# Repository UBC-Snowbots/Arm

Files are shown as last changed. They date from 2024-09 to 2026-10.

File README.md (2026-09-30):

# Arm – UBC Rover 

**CAD Models and Designs for the UBC Rover Arm**

## Table of Contents
1. [About](#about)  
2. [Repository Structure](#repository-structure)  
3. [Getting Started](#getting-started)  
4. [CAD Workflow & Tools](#cad-workflow--tools)  
5. [Contributing](#contributing)  
7. [Acknowledgments](#acknowledgments)  
8. [Contact](#contact)

---

## About
This repository contains the CAD models and design files for the 6 axis robotic arm of the UBC Rover, developed by the UBC Rover Arm subteam. These files are used for design iteration, simulation, and manufacturing preparation.

---

## Repository Structure
```
Arm/
├── Arm 2024-2025/       # CAD files for the 2024-2025 arm
├── Arm 2025-2026/       # CAD files for the 2025-2026 arm
├── Drawings/            # Technical drawings, schematics, and exports
├── .gitignore
└── README.md            # Project overview and documentation
```

- **Arm 2025-2026/**: Latest CAD sources & URDFs.
- **Drawings/**: Finished outputs such as PDFs, DXFs, and manufacturing diagrams.

---

## Getting Started

### Prerequisites
- CAD Software compatible with source files, currently using Solidworks 2023.
- CAD viewer or PDF reader to view exported files without full CAD tools.

### How to Use
1. Clone the repository:
   ```bash
   git clone https://github.com/UBC-Snowbots/Arm.git
   cd Arm
   ```
2. Navigate to:
   - `Arm 2024-2025/` for the latest CAD work.
   - `Drawings/` for schematics and PDFs.
3. Open files in your CAD software or a viewer.
   
Or, download the github desktop app.

---

## CAD Workflow & Tools
- Primary CAD platform: Solidworks 2023.
- Standard modeling practices:
    - Use hole wizard where applicable (tapped & clearance holes)
    - **For manufacturing fits see below**
      - For close fits (bearings, bushings, etc) in 3D prints, use ~1mm extra for tolerances.
      - For looser fits (a cover to slide over something, like a sleeve) in 3D prints, use ~1.5mm extra.
      - When machining, we can get ~±0.1mm pretty easily. If necessary, maybe ±0.05mm. If you're going to machine it you can go as tight as you want.
    - When making assemblies, please include fasteners, and when making threads, make the threads basic to help the assembly run faster.
    - Make sure all sketches are fully defined
    - Use equation tables & add multiple configurations if necessary
- When saving a file for 3D printing, save it as a .STEP file for higher print quality
- Give files descriptive names & ensure they're in the proper folders
---

## Contributing
Please push your changes & send a message to the discord when you do. This helps us keep track of what's happening and prevents peoples work from being lost. 
### Through command prompt
1. Make the change and ideally only edit the file you need to edit
2. If you see a file you didn't mean to edit, or just moved the camera around in an assembly, unselect that file
3. Commit with a clear message:
   ```bash
   git commit -m "Add <feature>: description"
   ```
4. Merge with main branch
5. Send a message to the discord w the files you changed

### Through Github Desktop
1. Make the change and ideally only edit the file you need to edit
2. Open the github desktop app 
3. If you see a file you didn't mean to edit, or just moved the camera around in an assembly, unselect that file
4. Write a semi-detailed description
5. Push the changes AND merge to main branch
6. Send a message to the discord w the files you changed

Ensure new CAD files include notes or documentation

---

## Acknowledgments
This was not designed by a single person, it's a multi year project with influences from the start of the team. Thanks to all current & past Rover arm team members.

Thanks to the entire team, especially software for making the arm work & chassis for making it useful. 

---

## Contact
For questions or feedback:
- **Arm Team Leads 2026-27** – *(William Banquier: william.banquier@gmail.com, Matt Yung: yungco44@gmail.com)*
- UBC Rover GitHub: [https://github.com/UBC-Snowbots](https://github.com/UBC-Snowbots)

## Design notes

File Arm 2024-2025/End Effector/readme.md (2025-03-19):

## EE Github Documentation

### Files

- Tool Changer Prototypes
    - Ball Bearing Mech Changer
    - Smartshift Mechanical Tool Changer
    - Magnet Sensor A1301-2
- Big Gripper
	- Gripper End Effector
	- Derivative of Last Year's End Effector
	- Folder also contains copy of 2024 (old) end effector -> as in the entire CAD
	- Folder also has a copy of the maxxon motor 
- Percision End Effector
	- CoreXY 
		- CoreXY for the end effector
		- Contains all housing and CAD 
	- Gripper Mechanism
		- Contains cad for the gripper mechanism
		- Contains cad for the actuator ("poking thingy" folder)

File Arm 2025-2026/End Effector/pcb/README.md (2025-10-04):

# End Effector PCB Sub-directory 

## Goals: 
1. Hold relevant PCB files for the end effector 
2. Store relevant PCB CAD files for the overall arm CAD
3. Store end effector testing / rnd PCB projects

## Directories:
[/EE-PCB](./EE-PCB)

[/CAD](./CAD)

[/RND](../../RnD/PCB)

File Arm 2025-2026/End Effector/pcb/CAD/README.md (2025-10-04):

## End Effector PCB CAD Folder 

Please note the CAD files that are here + where they are used

## CAD-LIST
- 
-
-
-
-

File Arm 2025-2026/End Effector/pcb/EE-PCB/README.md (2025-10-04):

This is a parent folder for the PCB files used within the end effector

## List of Project and Where the Board is Used on the EE
-
-
-
-
-
-
-

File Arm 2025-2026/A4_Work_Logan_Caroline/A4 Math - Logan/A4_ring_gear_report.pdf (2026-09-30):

## A4 Ring Gear Analysis

Note: the excel file is attached with this. Alter the red highlighted cells as needed.

### Assumptions

1. A4 is constrained, that is: no axial or radial loading on the motor when it is not rotating
2. Low friction
3. The center of mass of L2, the end effector, and the load are along A4

In short, I assume that A4 has to overcome the inertia of its rotor, L2, EE and the load, but it does not face any significant resisting torques from gravity or friction.

### Derivation

Let N = total gear ratio on A4 motor

Let J = total moment of inertia felt by the rotor

From the rotor:

Trotor = Jαrotor

The moment of inertia of the load felt by the rotor is reduced by a factor N² , thus:

Trotor =

Jrotor +

Jload
N²
αrotor | (1)

Also, due to the gear reduction:

αL2 =

αrotor
N

(2)

αL2 =

NTrotor

N²Jrotor + Jload

### Plugging in the Numbers

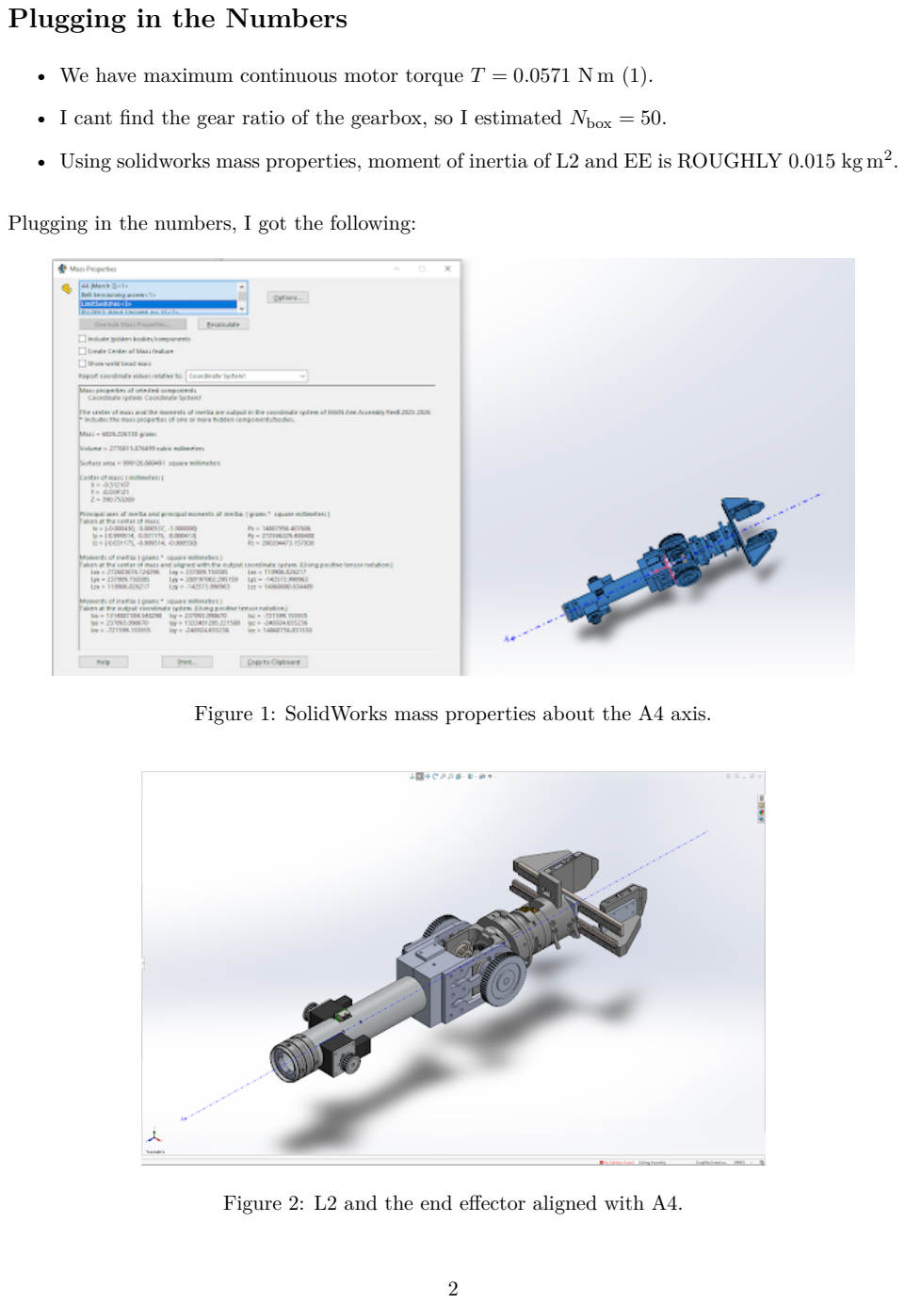
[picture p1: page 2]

- We have maximum continuous motor torque T = 0.0571 N m (1).
- I cant find the gear ratio of the gearbox, so I estimated Nbox = 50.
- Using solidworks mass properties, moment of inertia of L2 and EE is ROUGHLY 0.015 kg m² .

Plugging in the numbers, I got the following:

Figure 1: SolidWorks mass properties about the A4 axis.

Figure 2: L2 and the end effector aligned with A4.

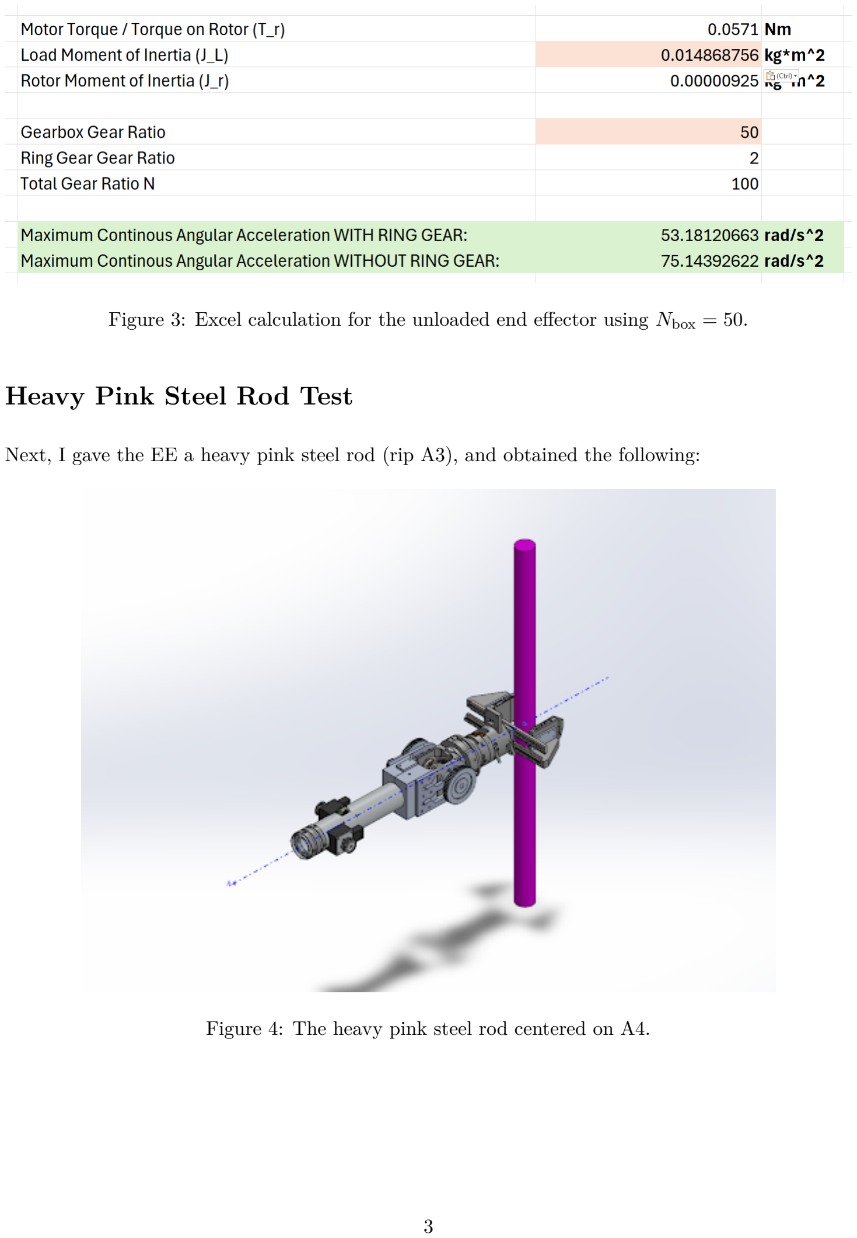
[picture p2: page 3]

Figure 3: Excel calculation for the unloaded end effector using Nbox = 50.

### Heavy Pink Steel Rod Test

Next, I gave the EE a heavy pink steel rod (rip A3), and obtained the following:

Figure 4: The heavy pink steel rod centered on A4.

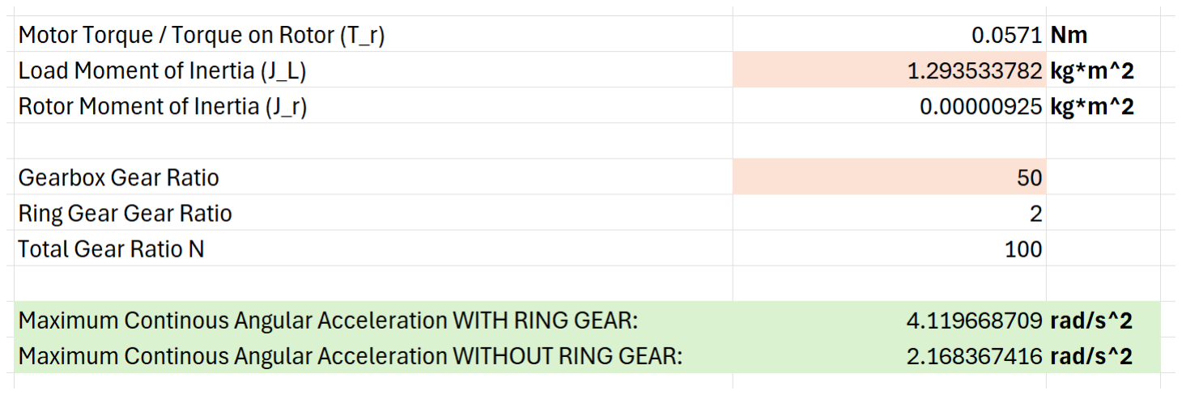
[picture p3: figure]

Figure 5: Excel calculation with the heavy steel rod using Nbox = 50.

### Conclusion

As long as Ngearbox ≥ 29, A4 is actually “quicker” WITHOUT the ring gear when the end effector is unloaded. However, the 2:1 ring gear begins to support A4 angular acceleration at higher loads.

With a known Ngearbox, one could easily use the excel calculator to pinpoint the exact load moment of inertia at which the ring gear becomes a useful support (ignoring the extra complexity).

### The Dangerous Assumption

Now, the astute among you may realize that assumption 3 is quite dangerous. For example, what if the pole was held like this?:

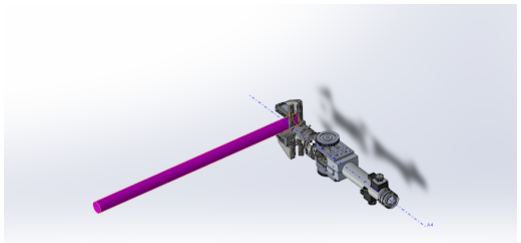
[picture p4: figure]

Figure 6: The same rod held asymmetrically about A4.

The rod moves the large center of mass away from A4, creating a resistive gravitational torque on A4. The A4 motor would be cooked.

The math here is pretty simple: by sacrificing the ring gear which has a gear ratio of 2:1, we are exactly reducing the maximum torque output of L2 by this factor of 2. In other words, the maximum asymmetrical load would halve, so to speak.

More specifically:

With a stall torque of 0.263 N m (1), the resistive torque on L2 can be no more than

τL2,max = (0.263 N m) × N,

where N is the total gear ratio from the motor to L2. For example, after removing the 2:1 ring-gear stage, N = 50, so this is about a single apple 9 meters away horizontally from the axis.

TL;DR

By removing the 2:1 ring-gear stage:

Pros:

1. The unloaded A4 angular acceleration is higher, ie A4 rotation is quicker
2. The theoretical maximum A4 angular speed is doubled for the same motor speed
3. Simpler design
4. No more unmeshing of ring gear due to A4 offset
5. Less backlash

Cons:

1. At higher loads, A4 angular acceleration is lower (exact load can be calculated in the attached spreadsheet)
2. The maximum allowable resistive torque on L2 due to friction and gravity is exactly halved. Likely to only be a problem for heavy asymmetric loads, such as distant apples.

Reference:

1. https://www.maxongroup.com/maxon/view/product/200142

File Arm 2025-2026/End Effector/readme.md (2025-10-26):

## End Effector :eyes:

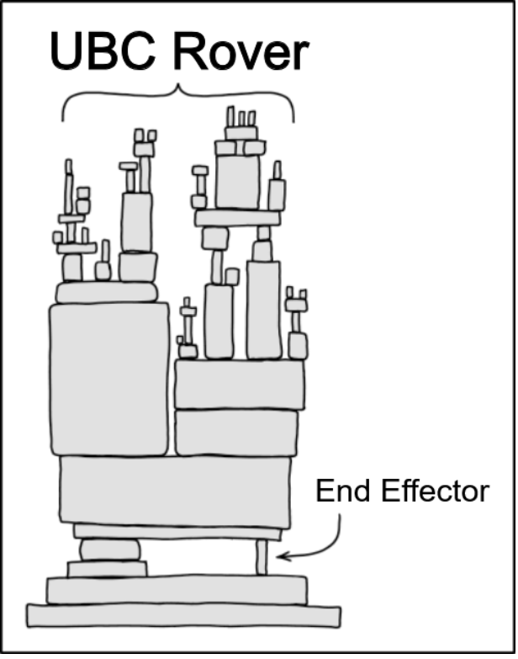
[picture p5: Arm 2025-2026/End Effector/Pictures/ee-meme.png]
EE Meme


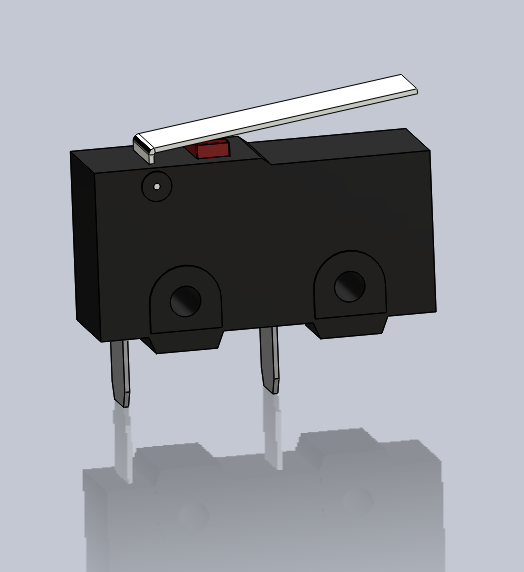
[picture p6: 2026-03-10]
Arm 2025-2026/End Effector/Polar Precision/OTS/Limit Switch/Limit A1.PNG

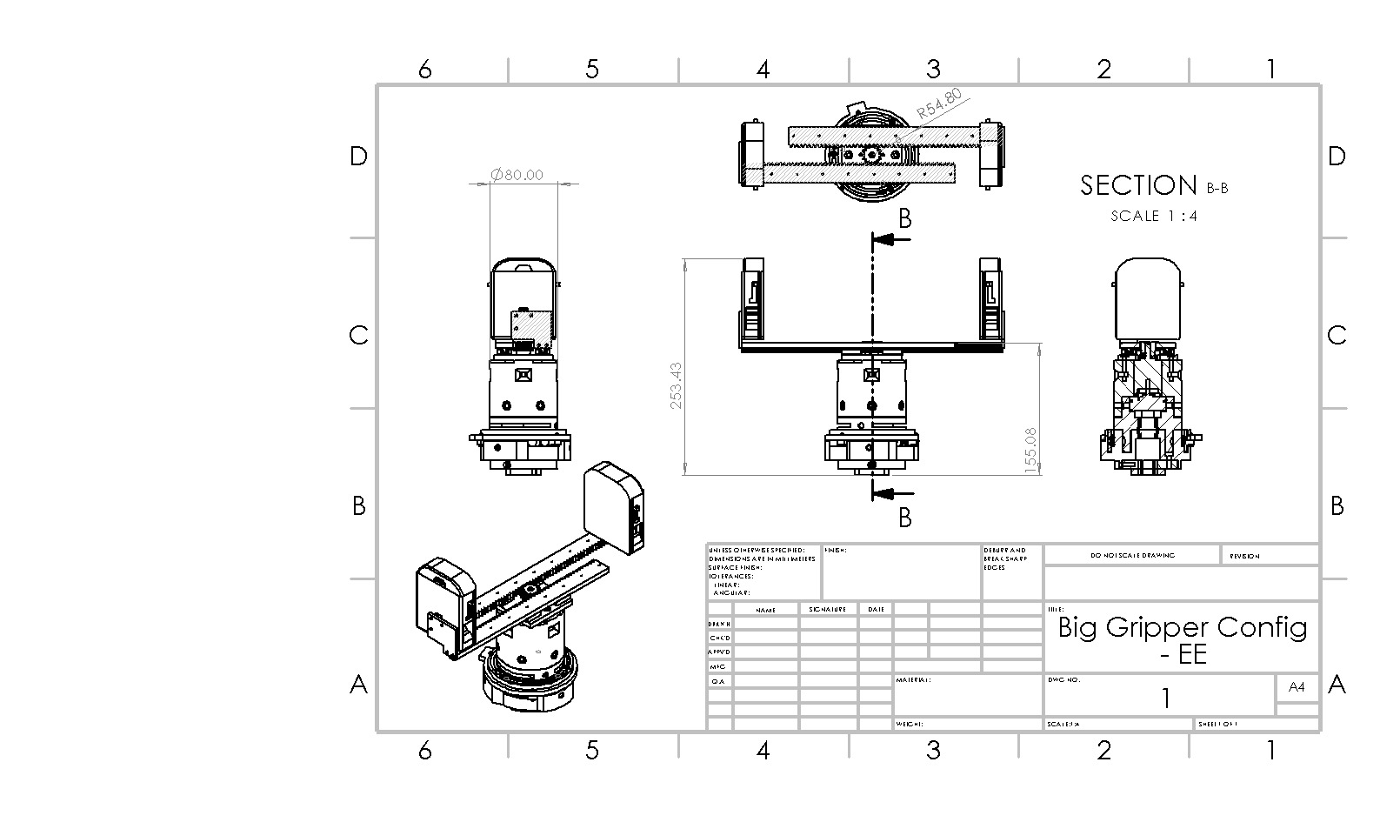
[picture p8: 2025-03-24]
Arm 2024-2025/End Effector/Tool Changer Prototypes/ball-bearing-mech-changer/Big Gripper Drawing.JPG

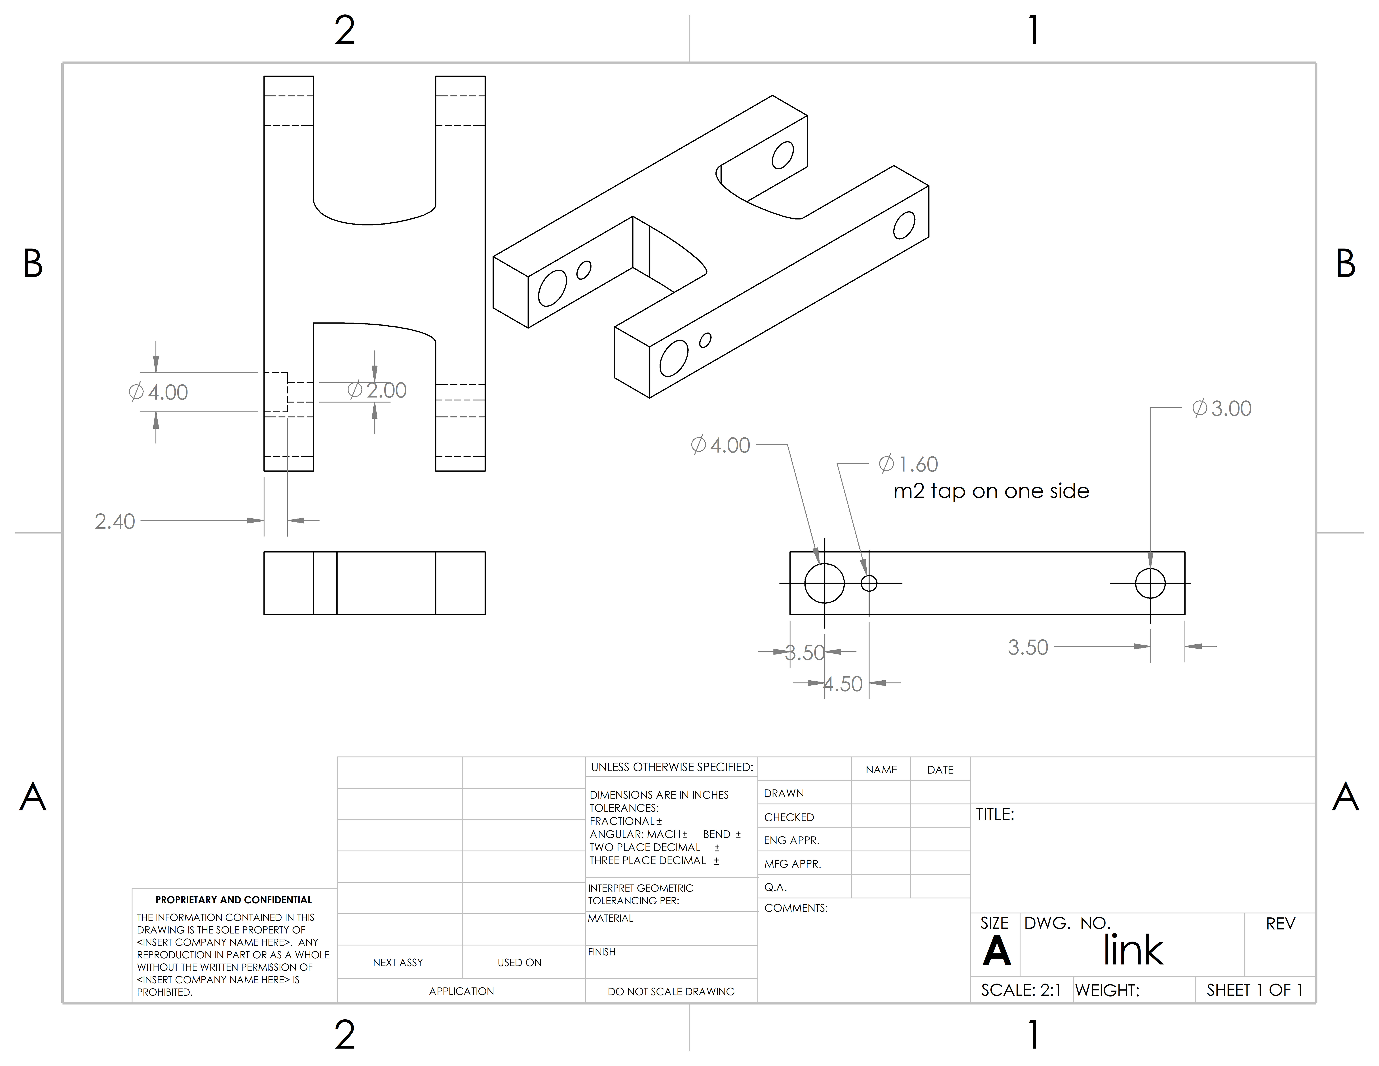
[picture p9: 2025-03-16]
Arm 2024-2025/End Effector/Precision End Effector/Gripper mechanism/waterjet/link.JPG

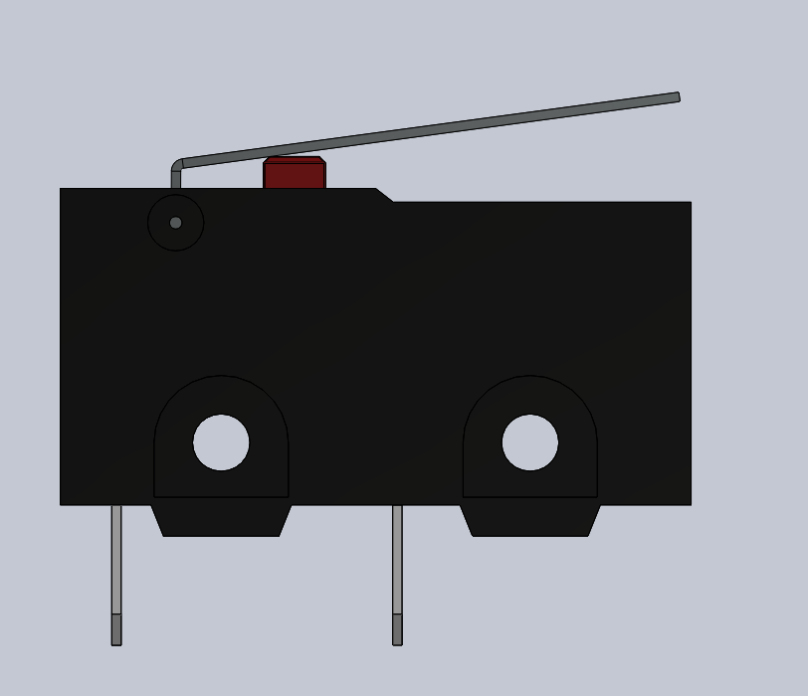
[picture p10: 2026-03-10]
Arm 2025-2026/End Effector/Polar Precision/OTS/Limit Switch/Limit A2.PNG

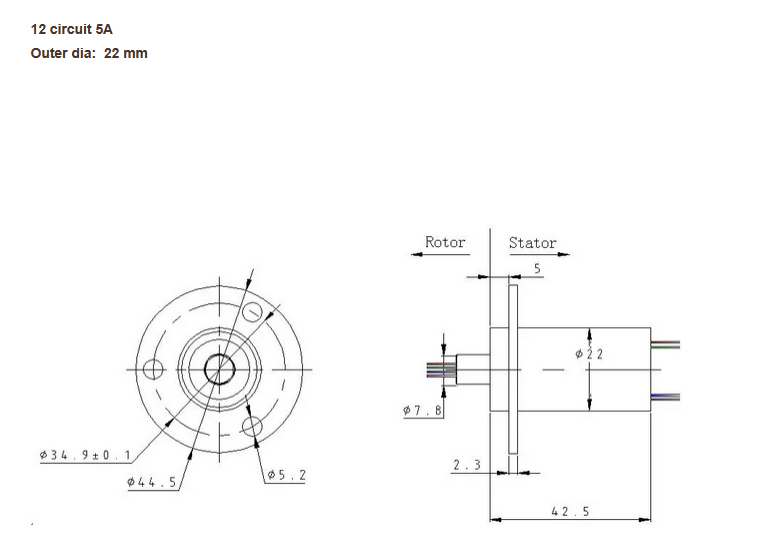
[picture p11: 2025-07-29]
Arm 2024-2025/Link 2/12circuit 5A Slip Ring.png

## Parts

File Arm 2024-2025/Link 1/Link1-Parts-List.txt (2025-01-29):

Corner Mount thing:

https://www.mcmaster.com/4844N108/

Ball-bearing for link 1 A2 harmonic drive:

https://www.mcmaster.com/6656K227/

Bearing for support A2:

https://www.mcmaster.com/5972K168/

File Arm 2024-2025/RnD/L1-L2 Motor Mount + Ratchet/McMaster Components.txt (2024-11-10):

Corner Mount thing:

https://www.mcmaster.com/4844N108/

Shaft Couple 6.35mm to 12mm:

https://www.amazon.ca/uxcell%C2%AE-Coupling-Diameter-Aluminum-Connector/dp/B06X9RZ1QC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

Ratchet gear:
https://www.mcmaster.com/6283K64/

Pawl:

https://www.mcmaster.com/6283K72/

Bushing:

https://www.mcmaster.com/6658K11/

Spring:

https://www.mcmaster.com/94125K414/

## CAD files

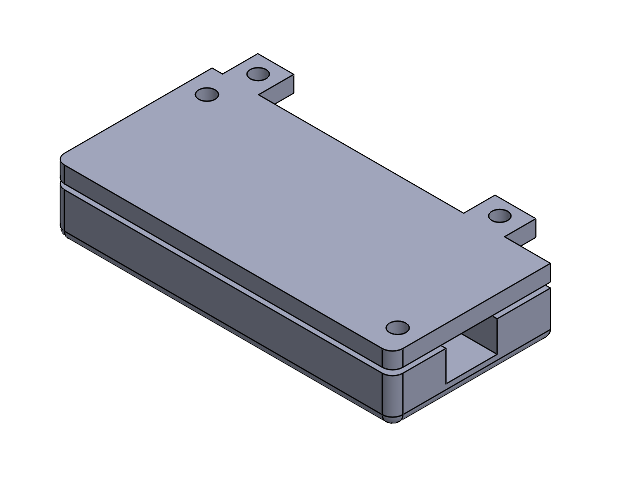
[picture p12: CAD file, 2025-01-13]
Arm 2024-2025/End Effector/Big Gripper/2024 End Effector/esp32/esp32_container_assembly.SLDASM
esp container
esp metal top

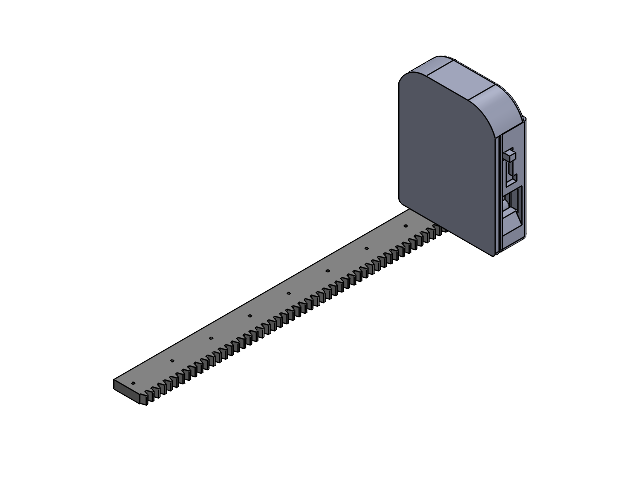
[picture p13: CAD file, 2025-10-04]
Arm 2024-2025/End Effector/Big Gripper/2024 End Effector/Fingers.SLDASM
SR1.5-300_On
Finger_Backing
base3
opener3 x 2
wall3 x 2
thing_inside_wall_3 x 2
top3
detachable3

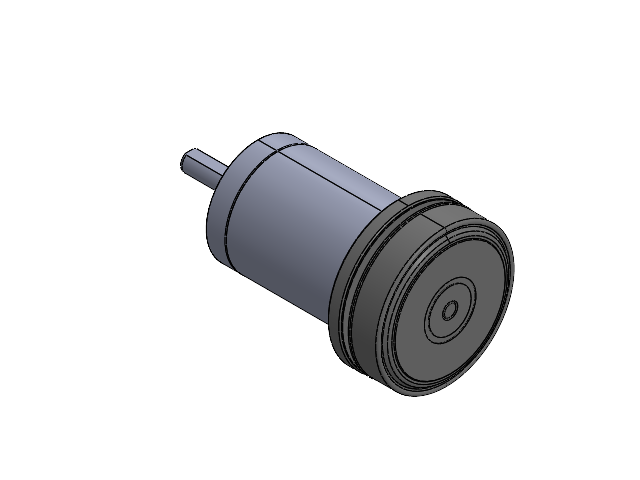
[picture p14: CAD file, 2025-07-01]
Arm 2024-2025/End Effector/Big Gripper/Big Gripper Motor Assy.SLDASM
Big Gripper Gearbox
Big Gripper Motor

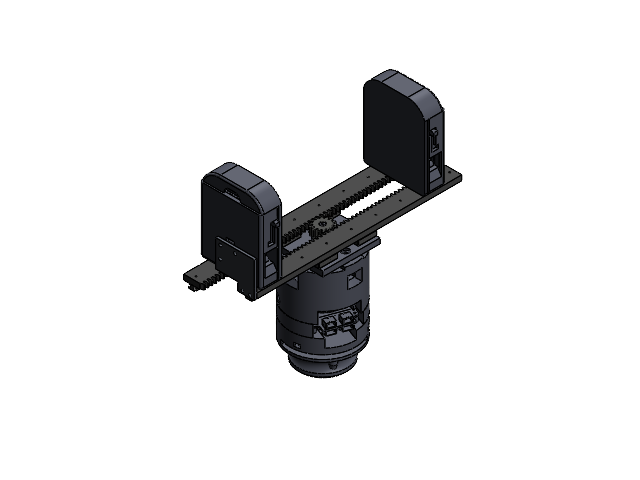
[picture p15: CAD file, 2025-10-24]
Arm 2024-2025/End Effector/Big Gripper/New attachment to tool changer/Assembly for big gripper attachment.SLDASM
plate for rail and motor attachment
Motor mount_BG
BIg_gripper_tool_attachment
9867K5_Sleeve Bearing Carriage x 4
Big Gripper Gearbox
Big Gripper Motor
SR1.5-300_On x 2
Finger_Backing x 2
base3 x 2
opener3 x 4
wall3 x 4
thing_inside_wall_3 x 4
top3 x 2
detachable3 x 2
9867K153_7 mm Wide x 250 mm Long Guide Rail for 17 mm Wide Sleeve Bearing Carriage x 2
SET-SCREW4-5
GEABB1.5-14-10-B-6_b
BT-0009
BT-0010
BT-0011
BT-0012
Moteus_thing
motor driver cover

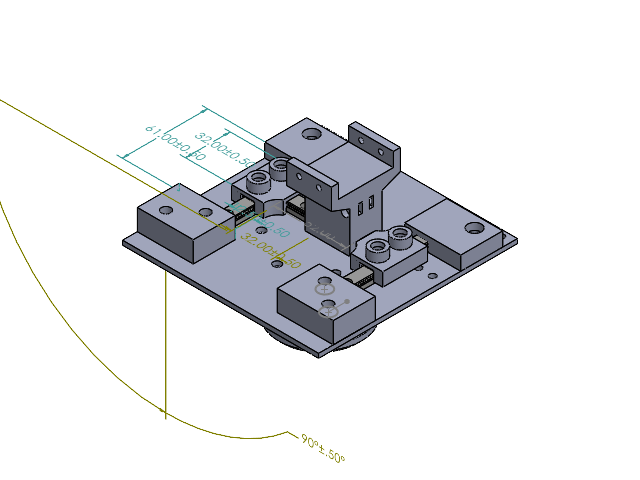
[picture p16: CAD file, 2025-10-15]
Arm 2024-2025/End Effector/Precision End Effector/Core-XY/Assemblies/Core XY Assembly Mk4.SLDASM
Corexy_baseplate_waterjet
6709K114_Ball Bearing Carriage x 3
6709K143_55 mm Long x 9 mm Wide Standard Guide Rail for Ball Bearing Carriage x 3
bearing housing x 2
Bottom left pivot housing
bottom right pivout housing
CoreXY_tool_attachment
top left motor housing
top right motor housing
bearing housing middle extended

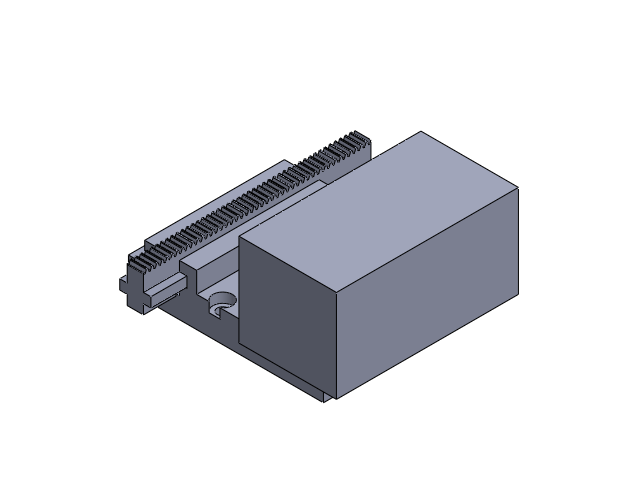
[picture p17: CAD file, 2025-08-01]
Arm 2024-2025/End Effector/Precision End Effector/Gripper mechanism/poking thingy/poking thingy assem.SLDASM
rack_mount_motor
2485N242_Metal Gear Rack - 20 Degree Pressure Angle

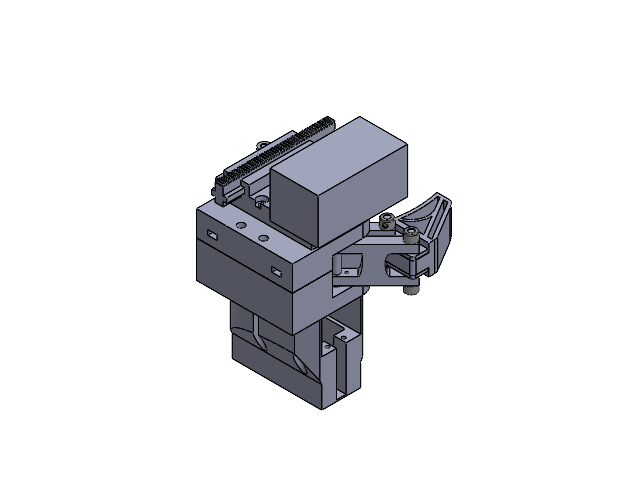
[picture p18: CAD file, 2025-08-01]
Arm 2024-2025/End Effector/Precision End Effector/Gripper mechanism/precision gripper assem.SLDASM
precision encloser
link x 4
gripper x 2
precision encloser-cap
Bearing624 x 8
4mm shaft 35mm x 8
6056N11_Carbon Steel Set Screw Collar x 8
6056N12_Carbon Steel Set Screw Collar x 2
servomotor mount
rack_mount_motor
2485N242_Metal Gear Rack - 20 Degree Pressure Angle
gripper shaft hole x 4
2664N318_Metal Gear - 20 Degree Pressure Angle x 2

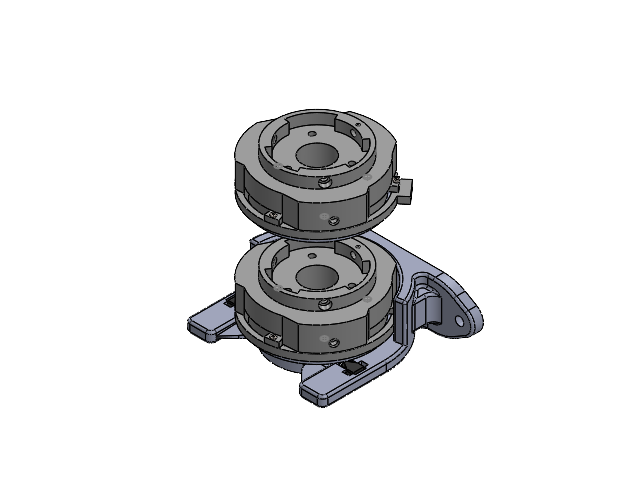
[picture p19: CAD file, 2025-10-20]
Arm 2024-2025/End Effector/Tool Changer Prototypes/ball-bearing-mech-changer/assembly/EE+tool_changer_assem.SLDASM
BT-0001 x 2
BT-0002 x 6
BT-0004 x 2
pan cross head_am x 12
hex nut style 1_am x 6
BT-0003 x 2
14mm ball-bearing x 12
CHASSIS MOUNT V2
WHEEL CASING [PLA] x 4
WHEEL CORE [PLA] x 2
WHEEL [TPU] x 2
BT-0005

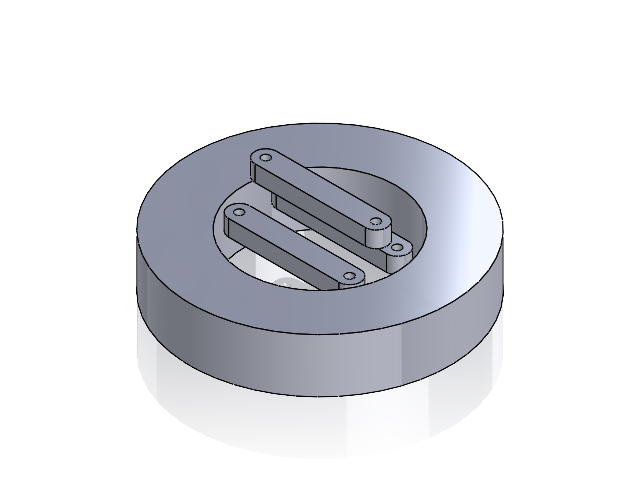
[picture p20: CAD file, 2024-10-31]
Arm 2024-2025/End Effector/Tool Changer Prototypes/PogoPin Spec/Mockup for sizing of PogoPins in Part.SLDASM
Holder
aliexpress 4-pin-screwhole x 3

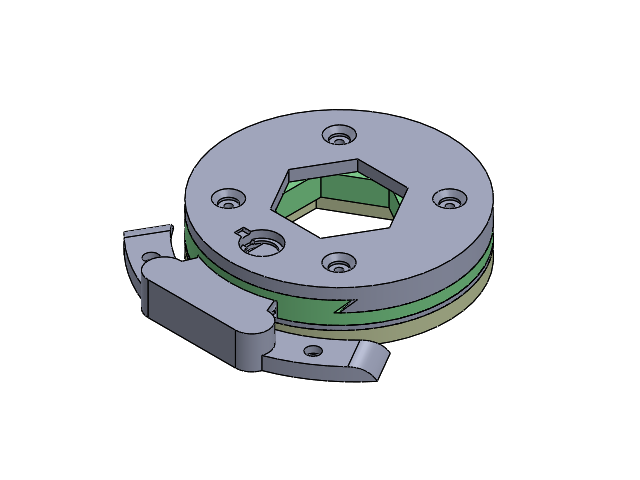
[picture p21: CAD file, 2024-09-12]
Arm 2024-2025/End Effector/Tool Changer Prototypes/Smartshift Mechanical Tool Changer Prototype/CAD/Combined Sliding Tool Changer.SLDASM
Bottom
Top
Bottom-Baseplate
BottomMagHolder
Sliding Magnet Holder
Side Insert For Magnet Holder
Attachment Point for Device

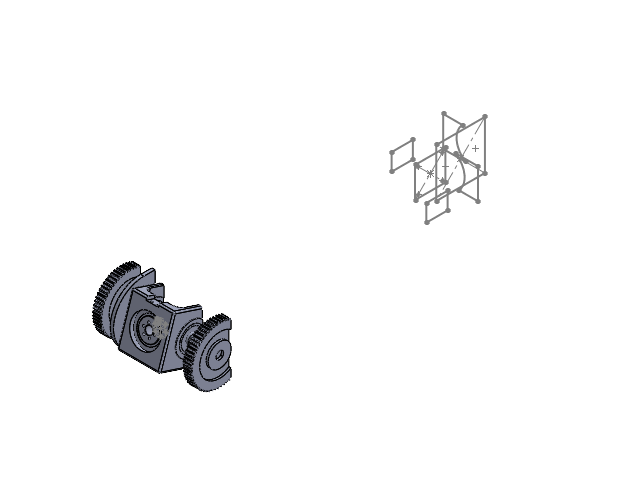
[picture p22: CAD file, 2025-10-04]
Arm 2024-2025/Link 2/Link2-Assem.SLDASM
link2_tube
Internal_Uprights
Bevel-Gear x 2
Bevel-Gear-MountingHoles
SDP_sdpsi_a_6a55-020df0908.stp x 2
bearing61808 x 3
bushing61808 x 3
bearing61802 x 2
sprocket-uprights x 2
DifferentialShaft x 2
12 mm retaining ring x 2
A56_gear x 2
A56_motor x 2
new_A56_spacer x 2
RV-0012_Wrist-Upright_Copy
A56_plate x 2
Wire Flange Tube

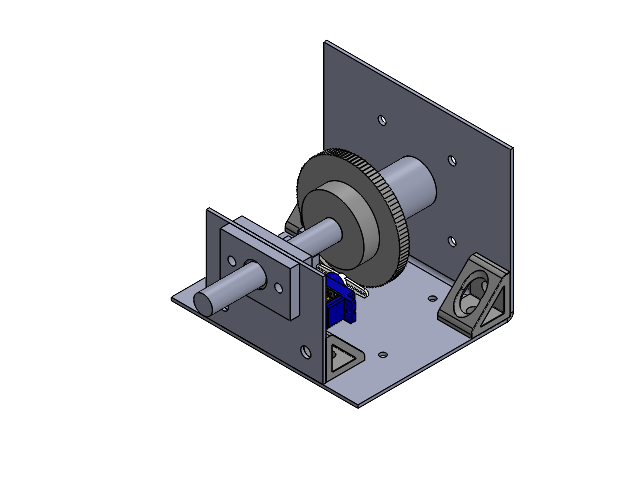
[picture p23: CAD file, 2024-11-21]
Arm 2024-2025/RnD/L1-L2 Motor Mount + Ratchet/L1-L2-Assembly.SLDASM
L1-L2-Motor-Bracket
25mm tall gusset x 4
Shaft-Couple
Shaft
6283K64_Metal Ratcheting Gear
6283K72_Pawl for 6 mm Wide Face Metal Ratcheting Gear
PowlMount
6658K11_Oil-Embedded 841 Bronze Sleeve Bearing
Shaft_Support
Bushing_Support x 2
SG90 - Micro Servo 9g - Tower Pro.1
SG90 - Micro Servo 9g - Tower Pro.3
SG90 - Micro Servo 9g - Tower Pro.6

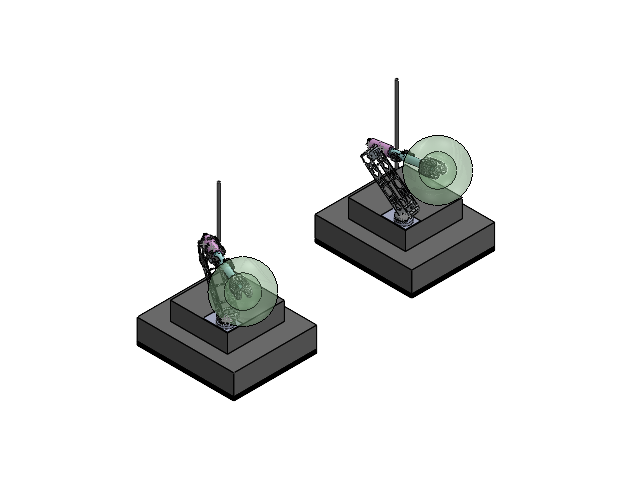
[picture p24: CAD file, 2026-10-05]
Arm 2025-2026/A4_Work_Logan_Caroline/Arms_On_Chassis/full_rover.SLDASM
the_chassis x 2
simplified_base_plate x 2
Link1-Support-Side_SHORTENED
Link1-Harm-Side_SHORTENED
threaded_ring x 2
bearing_support x 2
revised motorhousing x 2
2800-0004-0014_90128A207 x 4
6656K146_Steel Ball Bearing
L2_Bearing_Shim x 2
A4_Brace x 2
Bearing_Clamp_Piece
Bearing_Clamp_PIece_2
Bearing_Clamp_Piece_3
bearing_clamp x 2
cover_3
A1-Plate
KA CIRC POC SEPARATOR SAMPLE_02610025-0.step x 4
KA SIZE CATALOG BALL_KA025.step x 176
KA INNER CATALOG_KA025003.step x 4
KA OUTER ANGULAR CONTACT CATALOG_KA025A02.step x 4
link2_tube x 2
A56_gear x 6
A56_motor x 6
Cross-Bracing x 6
new_A56_spacer x 4
EC90fl-160W-586655.stp x 2
A3-Motor-Harm-Intermediate x 2
outside_CSF-17-xxx-2UH-ULW_fixed.stp x 2
outside_CSF-17-xxx-2UH-ULW-WG.stp x 2
outside_CSF-17-xxx-2UH-ULW_output.stp x 2
A3-Harm-Link1-Intermediate x 2
A1-Side-Plate-Support x 4
A1-Side-Plate-Crosslink x 4
RV-0013_Wrist-Upright_no_LS x 2
RV-0013_Wrist-Upright x 2
uprights_cutouts x 4
A56_plate x 4
socket_screw_m4 x 24
screw_support x 8
A4_Holder x 6
the_unfaithful_end_effector
Link1-Support-Side
Link1-Harm-Side
cover_3_faithful
SHITTY_ADAPTER_DESIGN
A1-Plate_faithful
A2-Side-Plate-Crosslink x 2
the_end_effector

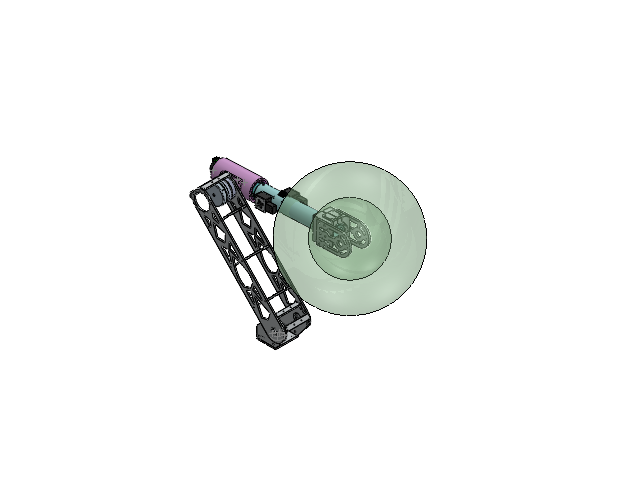
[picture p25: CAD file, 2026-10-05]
Arm 2025-2026/A4_Work_Logan_Caroline/V5_faithful/__FAITHFUL_ASSEMBLY__.SLDASM
Link1-Support-Side
Link1-Harm-Side
link2_tube
A56_gear x 3
threaded_ring
bearing_support
revised motorhousing
2800-0004-0014_90128A207 x 2
L2_Bearing_Shim
bearing_clamp
cover_3_faithful
SHITTY_ADAPTER_DESIGN
A1-Plate_faithful
screw_support x 4
socket_screw_m4 x 12
uprights_cutouts x 2
RV-0013_Wrist-Upright_no_LS
RV-0013_Wrist-Upright
A56_motor x 3
A56_plate x 2
new_A56_spacer x 2
KA CIRC POC SEPARATOR SAMPLE_02610025-0.step x 2
KA SIZE CATALOG BALL_KA025.step x 88
KA INNER CATALOG_KA025003.step x 2
KA OUTER ANGULAR CONTACT CATALOG_KA025A02.step x 2
EC90fl-160W-586655.stp
A3-Motor-Harm-Intermediate
outside_CSF-17-xxx-2UH-ULW_fixed.stp
outside_CSF-17-xxx-2UH-ULW-WG.stp
outside_CSF-17-xxx-2UH-ULW_output.stp
A3-Harm-Link1-Intermediate
Cross-Bracing x 3
A1-Side-Plate-Support x 2
A1-Side-Plate-Crosslink x 2
A2-Side-Plate-Crosslink x 2
the_end_effector

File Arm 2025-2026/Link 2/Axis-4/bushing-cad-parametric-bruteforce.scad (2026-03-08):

module hollow_ring_2d(inner_d, outer_d) {
    difference() {
        circle(d = outer_d, $fn = 200);
        circle(d = inner_d, $fn = 200);
    }
}

inner_base = 34 - 0.05;
outer_base = 40 + 0.05;
spacing = 45;

for (row = [0:2]) {
    for (col = [0:2]) {
        inner_d = inner_base - 0.05 * col;
        outer_d = outer_base + 0.05 * row;

        translate([col * spacing, row * spacing])
            hollow_ring_2d(inner_d, outer_d);
    }
}

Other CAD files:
Arm 2025-2026/A4_Work_Logan_Caroline/V5_unfaithful/__UNFAITHFUL_ASSEMBLY__.SLDASM
Arm 2025-2026/Arm-Stand/Arm-Stand.SLDASM
Arm 2025-2026/End Effector/Big Gripper/2024 End Effector/Fingers.SLDASM
Arm 2025-2026/End Effector/Big Gripper/Finger pad - 06.27.2024/arm_dexterity_tools/hex_key_holder.SLDASM
Arm 2024-2025/Arm URDF/meshes/a1_shoulder_base.STL
Arm 2024-2025/Arm URDF/meshes/a2_link_1.STL
Arm 2024-2025/Arm URDF/meshes/a3_axis4_housing.STL
Arm 2024-2025/Arm URDF/meshes/a4_link2.STL
Arm 2024-2025/Arm URDF/meshes/a5_internal_upright.STL
Arm 2024-2025/Arm URDF/meshes/a6_EE_holder.STL
Arm 2024-2025/Arm URDF/meshes/base_link.STL
Arm 2024-2025/ArmPlateShim.SLDPRT
Arm 2024-2025/DriverHolder/DM320.SLDPRT
Arm 2024-2025/DriverHolder/DM320Frame.SLDPRT
Arm 2024-2025/DriverHolder/DM320Holder.SLDPRT
Arm 2024-2025/DriverHolder/DM542.SLDPRT
Arm 2024-2025/DriverHolder/DM542Frame.SLDPRT
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

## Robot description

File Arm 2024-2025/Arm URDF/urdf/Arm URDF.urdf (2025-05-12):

<?xml version="1.0" encoding="utf-8"?>
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
<robot name="Arm URDF">
  <link name="base_link">
    <inertial>
      <origin xyz="0.102260898282908 0.00311121926014173 -0.156019155205669" rpy="0 0 0" />
      <mass value="0.464292173847851" />
      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
    </inertial>
    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
  </link>
  <link name="a1_shoulder_base">
    <inertial>
      <origin xyz="0.00378215343885442 -0.0301295143675391 0.0522485793592078" rpy="0 0 0" />
      <mass value="0.742438926040346" />
      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
    </inertial>
    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
  </link>
  <joint name="shoulder_joint" type="revolute">
    <origin xyz="0.102000000000005 0.199999999999999 0.0377499999999958" rpy="0 0 -3.14159265358979" />
    <parent link="base_link" />
    <child link="a1_shoulder_base" />
    <axis xyz="0 0 1" />
    <limit lower="0" upper="3.14" effort="0" velocity="0" />
  </joint>
  <link name="a2_link_1">
    <inertial>
      <origin xyz="-0.31663624842113 -1.47449210178979E-05 -0.00360815454079563" rpy="0 0 0" />
      <mass value="1.94678380458644" />
      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
    </inertial>
    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
  </link>
  <joint name="link_1_joint" type="revolute">
    <origin xyz="0.00282500000000498 -0.0450000000000385 0.074999999999904" rpy="1.5707963267949 0 -1.5707963267949" />
    <parent link="a1_shoulder_base" />
    <child link="a2_link_1" />
    <axis xyz="0 0 1" />
    <limit lower="-3.14" upper="0" effort="0" velocity="0" />
  </joint>
  <link name="a3_axis4_housing">
    <inertial>
      <origin xyz="0.0408050572850942 0.0166036738004918 0.013626708114375" rpy="0 0 0" />
      <mass value="0.258864677478161" />
      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
    </inertial>
    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
  </link>
  <joint name="link1_link2" type="revolute">
    <origin xyz="-0.50000048929394 0 -0.0677177243260161" rpy="0 1.5707963267949 0" />
    <parent link="a2_link_1" />
    <child link="a3_axis4_housing" />
    <axis xyz="-1 0 0" />
    <limit lower="0" upper="3.14" effort="0" velocity="0" />
  </joint>
  <link name="a4_link2">
    <inertial>
      <origin xyz="0.136030828721491 0.000546842367514622 -4.51545797446572E-06" rpy="0 0 0" />
      <mass value="1.31628289409256" />
      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
    </inertial>
    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
  </link>
  <joint name="a4_rotation" type="revolute">
    <origin xyz="0.0451078368209206 0.205024453664939 0.223589169838865" rpy="-1.5707963267949 -0.828683805160042 1.5707963267949" />
    <parent link="a3_axis4_housing" />
    <child link="a4_link2" />
    <axis xyz="-1 0 0" />
    <limit lower="-1.57" upper="1.57" effort="0" velocity="0" />
  </joint>
  <link name="a5_internal_upright">
    <inertial>
      <origin xyz="0.0267788794933879 0.00778879051640191 0.00761484691204106" rpy="0 0 0" />
      <mass value="0.155027470866593" />
      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
    </inertial>
    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
  </link>
  <joint name="a5_rotation" type="revolute">
    <origin xyz="0.31694 0 0.024001" rpy="0.74211 1.5708 0" />
    <parent link="a4_link2" />
    <child link="a5_internal_upright" />
    <axis xyz="1 0 0" />
    <limit lower="-3.14" upper="3.14" effort="0" velocity="0" />
  </joint>
  <link name="a6_EE_holder">
    <inertial>
      <origin xyz="0.0227263684366685 -2.15736821771728E-05 -1.75136141242378E-05" rpy="0 0 0" />
      <mass value="0.268420822776766" />
      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
    </inertial>
    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
  </link>
  <joint name="a6_rotation" type="continuous">
    <origin xyz="0.024 0.031992 0.030931" rpy="-1.5708 -0.76854 1.5708" />
    <parent link="a5_internal_upright" />
    <child link="a6_EE_holder" />
    <axis xyz="-1 0 0" />
    <limit lower="0" upper="0" effort="0" velocity="0" />
  </joint>
</robot>

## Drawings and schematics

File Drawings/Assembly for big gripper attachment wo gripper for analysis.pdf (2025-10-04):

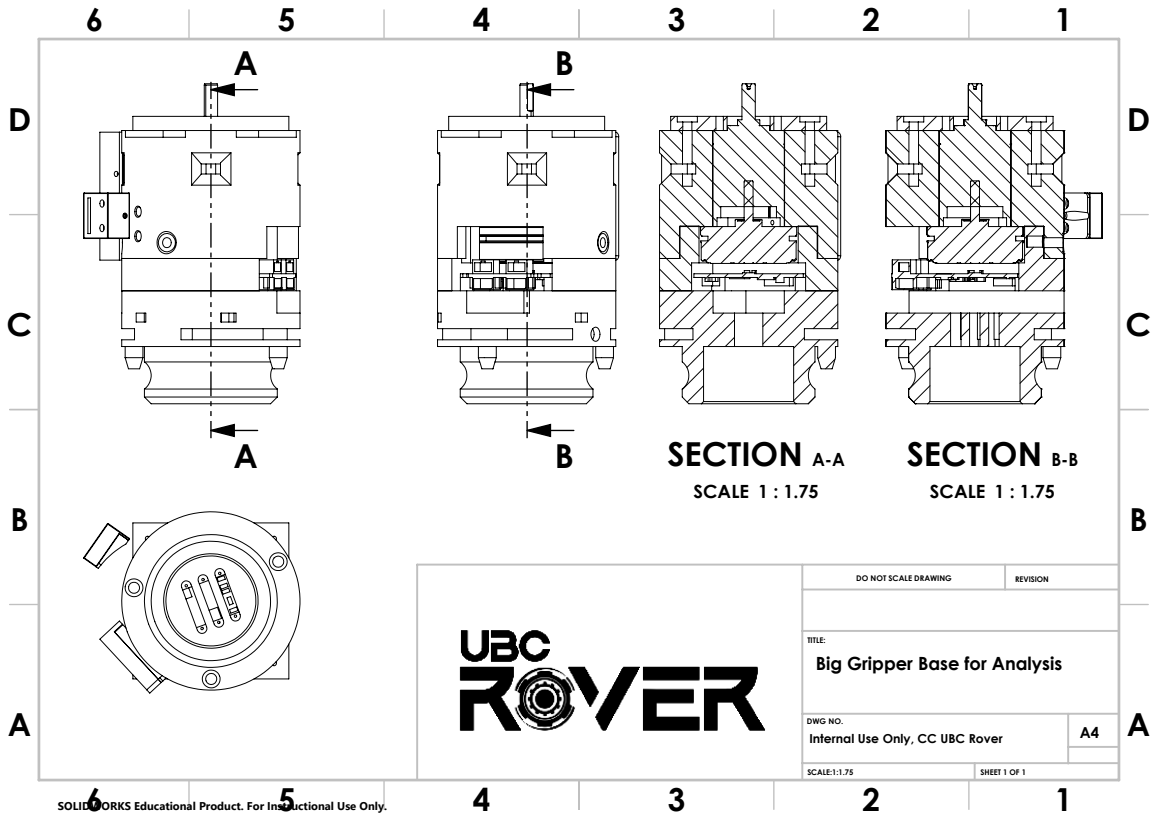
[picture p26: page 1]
B SECTION A-A; SCALE 1 : 1.75; SECTION B-B; SCALE 1 : 1.75 B B; DO NOT SCALE DRAWING; REVISION

TITLE:
Big Gripper Base for Analysis

SOLIDWORKS Educational Product. For Instructional Use Only.

DWG NO. | A4 Internal Use Only, CC UBC Rover

SCALE:1:1.75 | SHEET 1 OF 1

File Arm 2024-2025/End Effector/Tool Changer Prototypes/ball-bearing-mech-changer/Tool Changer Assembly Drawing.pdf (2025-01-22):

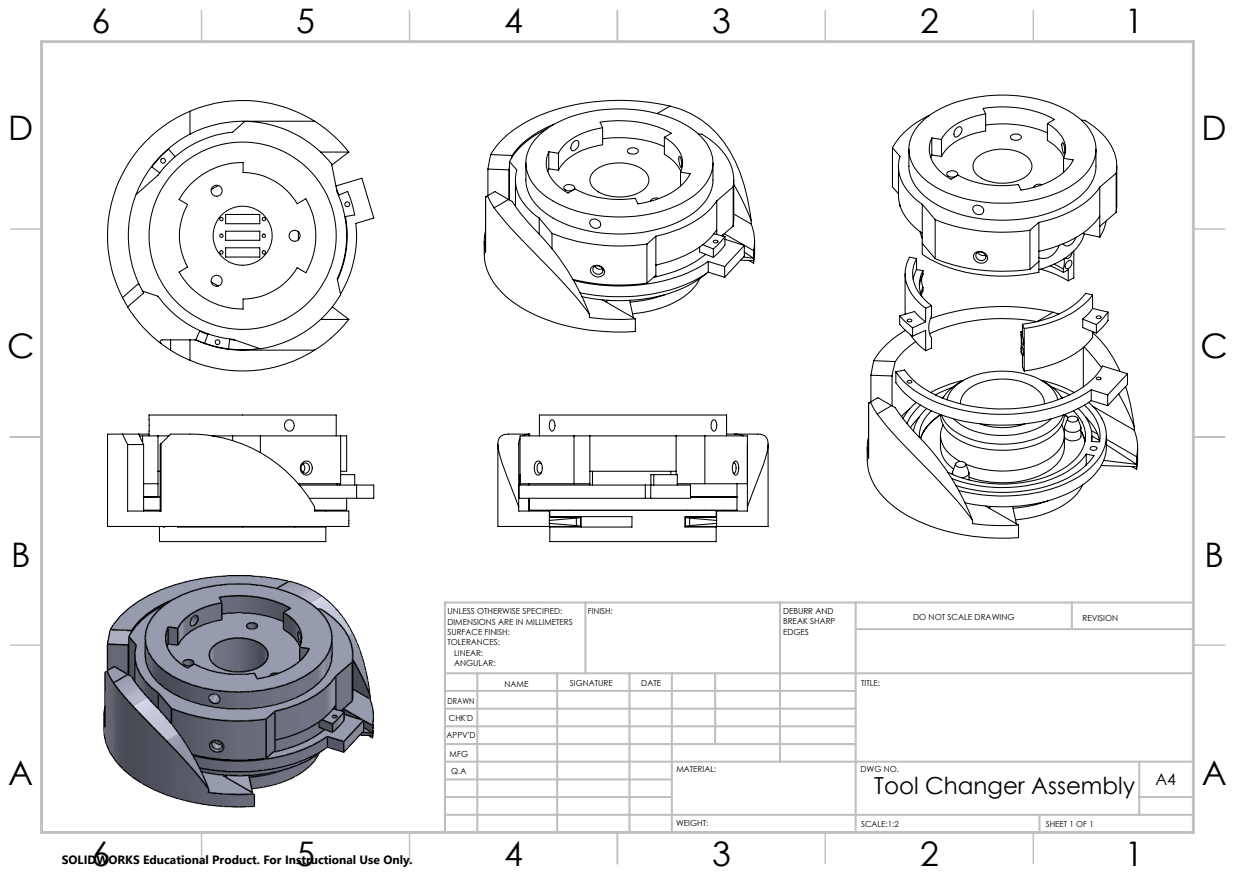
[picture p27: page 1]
FINISH:; DEBURR AND; BREAK SHARP; DO NOT SCALE DRAWING; REVISION; SCALE:1:2; SHEET 1 OF 1

UNLESS OTHERWISE SPECIFIED:
DIMENSIONS ARE IN MILLIMETERS
SURFACE FINISH:
TOLERANCES:
LINEAR:
ANGULAR:

NAME | SIGNATURE | DATE | | | | TITLE:

DRAWN
CHK'D
APPV'D
MFG
Q.A | | | | MATERIAL: | DWG NO. Tool Changer Assembly | A4

SOLIDWORKS Educational Product. For Instructional Use Only.

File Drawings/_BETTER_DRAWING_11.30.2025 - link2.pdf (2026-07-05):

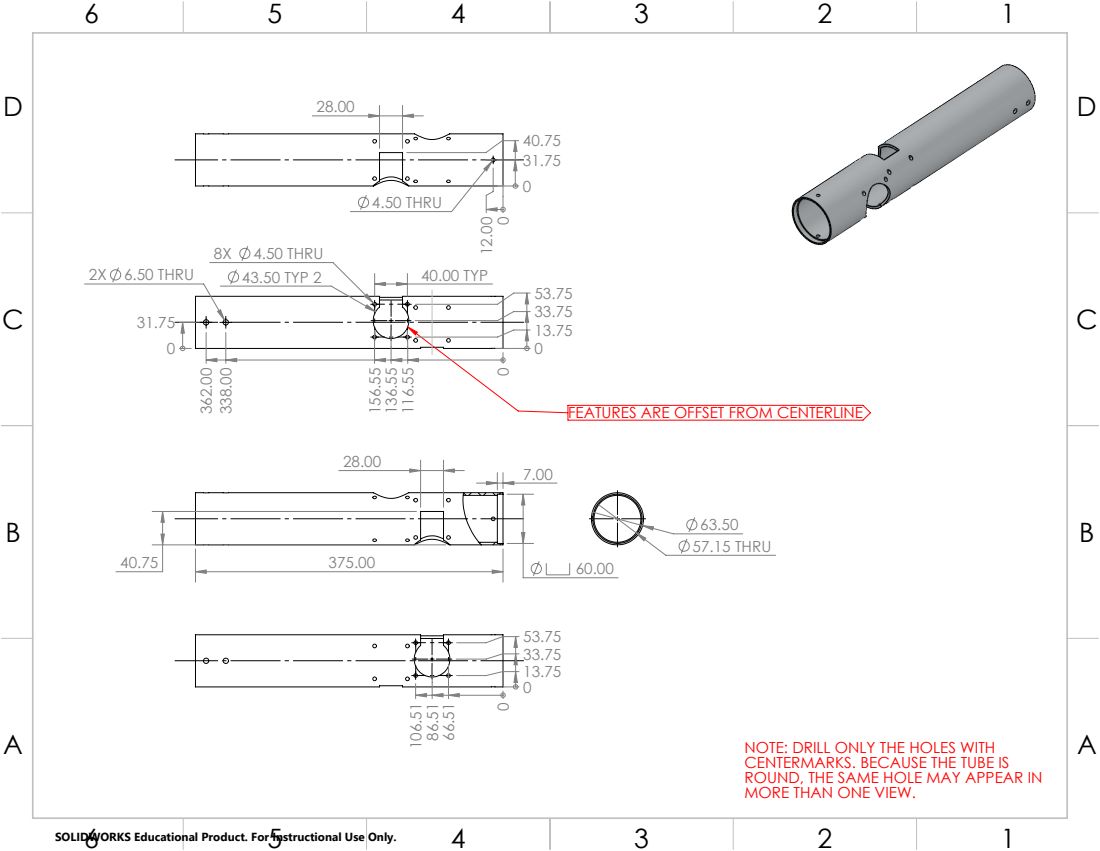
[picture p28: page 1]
2X 6.50 THRU; 8X 4.50 THRU; 43.50 TYP 2; 40.00 TYP; 4.50 THRU; 57.15 THRU

FEATURES ARE OFFSET FROM CENTERLINE

NOTE: DRILL ONLY THE HOLES WITH
CENTERMARKS. BECAUSE THE TUBE IS
ROUND, THE SAME HOLE MAY APPEAR IN
MORE THAN ONE VIEW.

SOLIDWORKS Educational Product. For Instructional Use Only.

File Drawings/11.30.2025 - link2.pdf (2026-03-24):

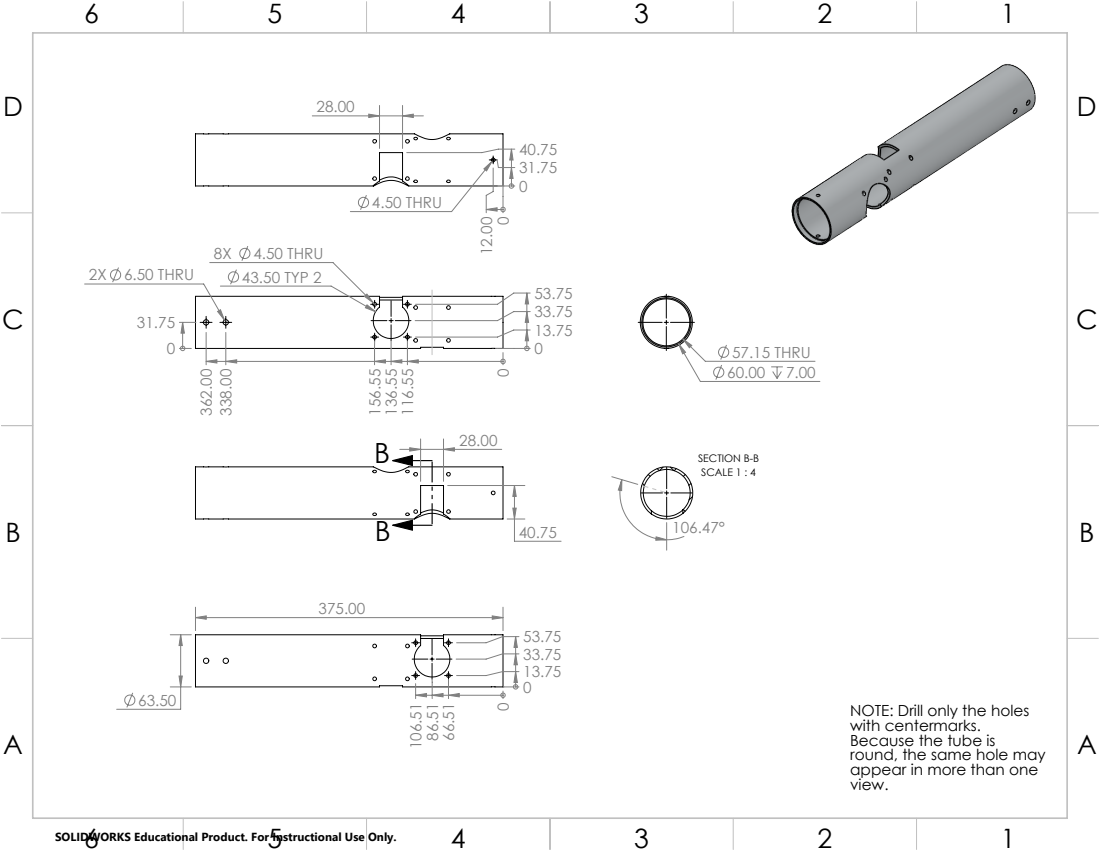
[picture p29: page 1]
2X 6.50 THRU; 8X 4.50 THRU 43.50 TYP 2; 4.50 THRU; 57.15 THRU 60.00 7.00; SECTION B-B SCALE 1 : 4

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

SOLIDWORKS Educational Product. For Instructional Use Only.

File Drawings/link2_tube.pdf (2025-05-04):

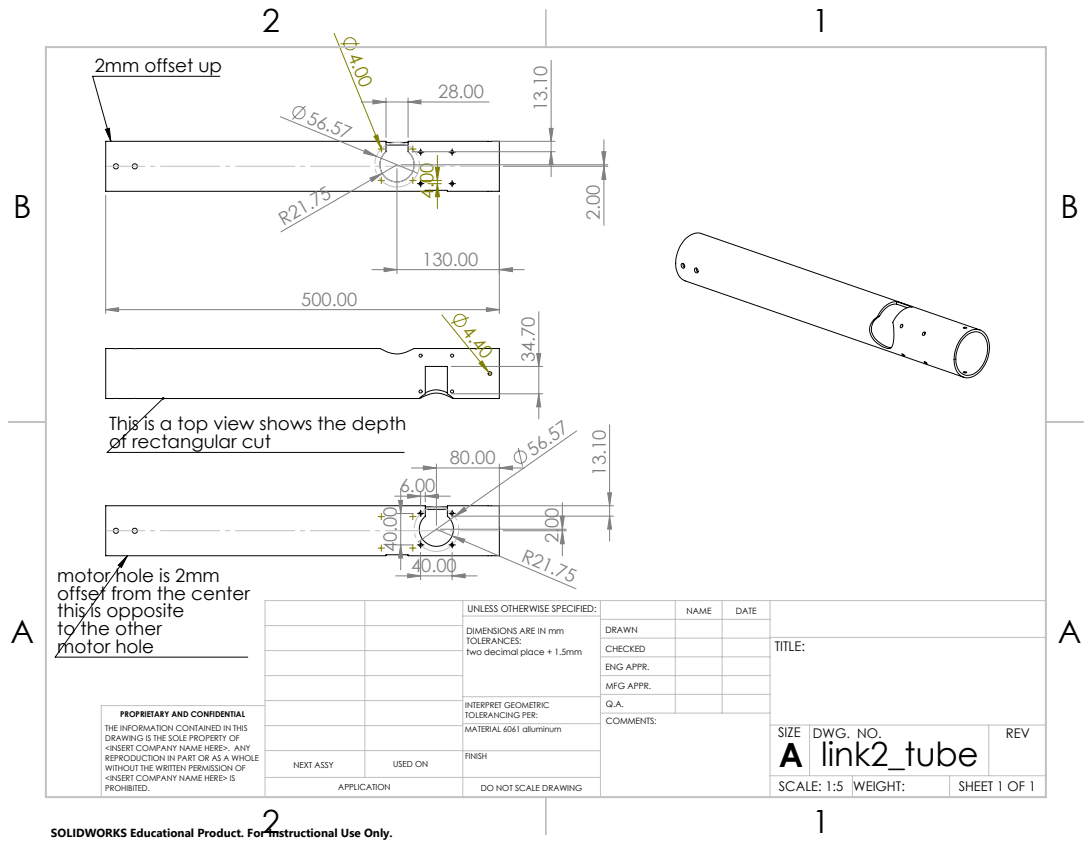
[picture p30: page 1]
2mm offset up; to the other A; motor hole

This is a top view shows the depth
of rectangular cut

motor hole is 2mm
offset from the center
this is opposite

UNLESS OTHERWISE SPECIFIED: | | NAME | DATE
DIMENSIONS ARE IN mm TOLERANCES: two decimal place + 1.5mm | DRAWN

CHECKED | | | TITLE:

ENG APPR.
MFG APPR.

INTERPRET GEOMETRIC TOLERANCING PER: | Q.A.
MATERIAL 6061 alluminum | | SIZE A | DWG. NO. link2_tube | REV

PROPRIETARY AND CONFIDENTIAL
THE INFORMATION CONTAINED IN THIS
DRAWING IS THE SOLE PROPERTY OF
<INSERT COMPANY NAME HERE>. ANY
REPRODUCTION IN PART OR AS A WHOLE
WITHOUT THE WRITTEN PERMISSION OF
<INSERT COMPANY NAME HERE> IS
PROHIBITED.

NEXT ASSY | USED ON | FINISH

APPLICATION | DO NOT SCALE DRAWING | | SCALE: 1:5 | WEIGHT: | SHEET 1 OF 1

SOLIDWORKS Educational Product. For Instructional Use Only.

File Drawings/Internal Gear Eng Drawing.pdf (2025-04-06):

B B

2

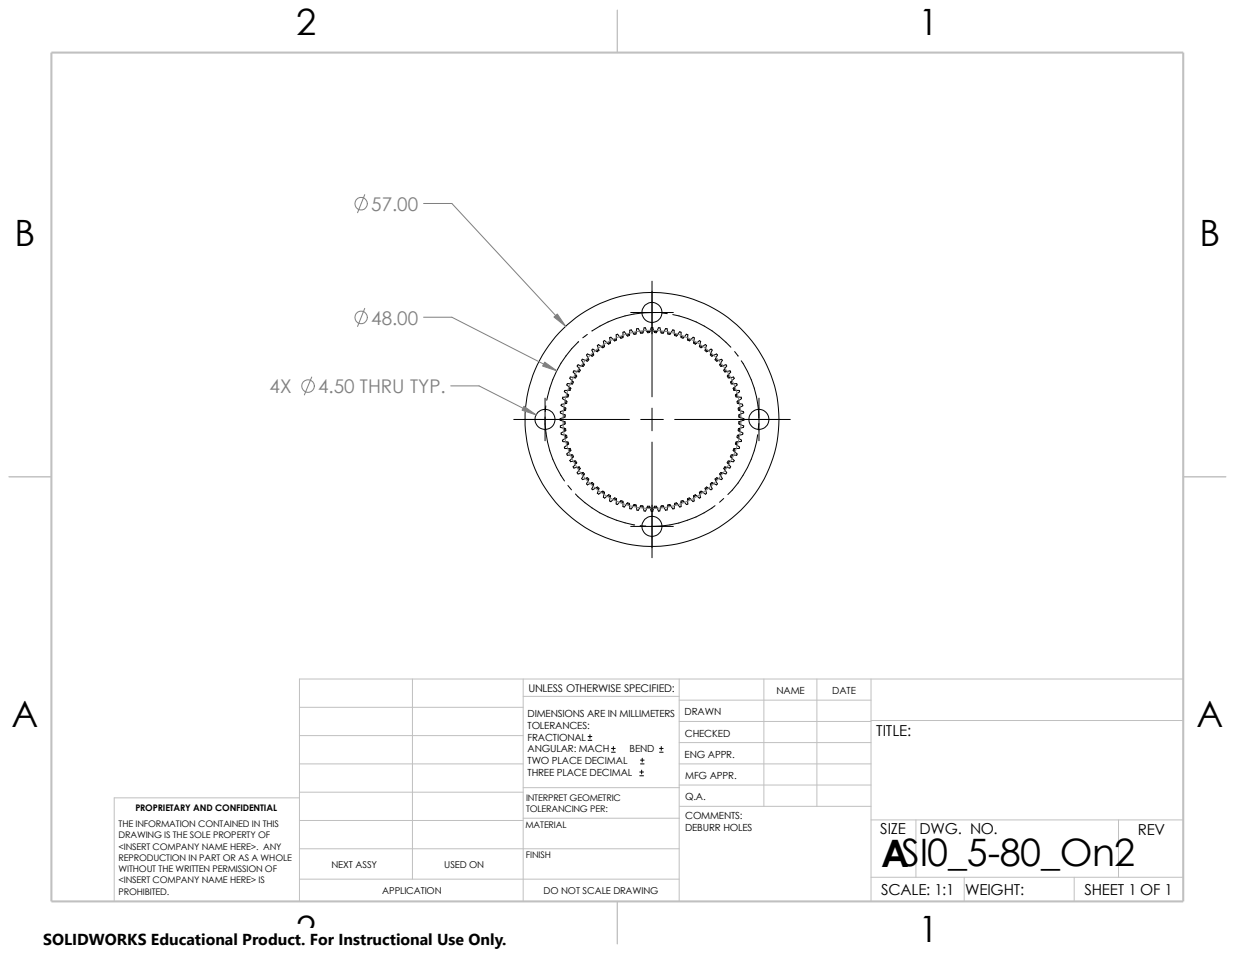
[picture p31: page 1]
DEBURR HOLES; COMMENTS:; INTERPRET GEOMETRIC; PROPRIETARY AND CONFIDENTIAL; TOLERANCING PER:; 4X 4.50 THRU TYP.

UNLESS OTHERWISE SPECIFIED: | | NAME | DATE

DIMENSIONS ARE IN MILLIMETERS TOLERANCES: FRACTIONAL ANGULAR: MACH BEND TWO PLACE DECIMAL THREE PLACE DECIMAL | DRAWN

CHECKED | | | TITLE:

ENG APPR.
MFG APPR.

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

MATERIAL | | SIZE A SI0_5-80_On2 | DWG. NO. | REV

NEXT ASSY | USED ON | FINISH

APPLICATION | DO NOT SCALE DRAWING | | SCALE: 1:1 | WEIGHT: | SHEET 1 OF 1

SOLIDWORKS Educational Product. For Instructional Use Only.

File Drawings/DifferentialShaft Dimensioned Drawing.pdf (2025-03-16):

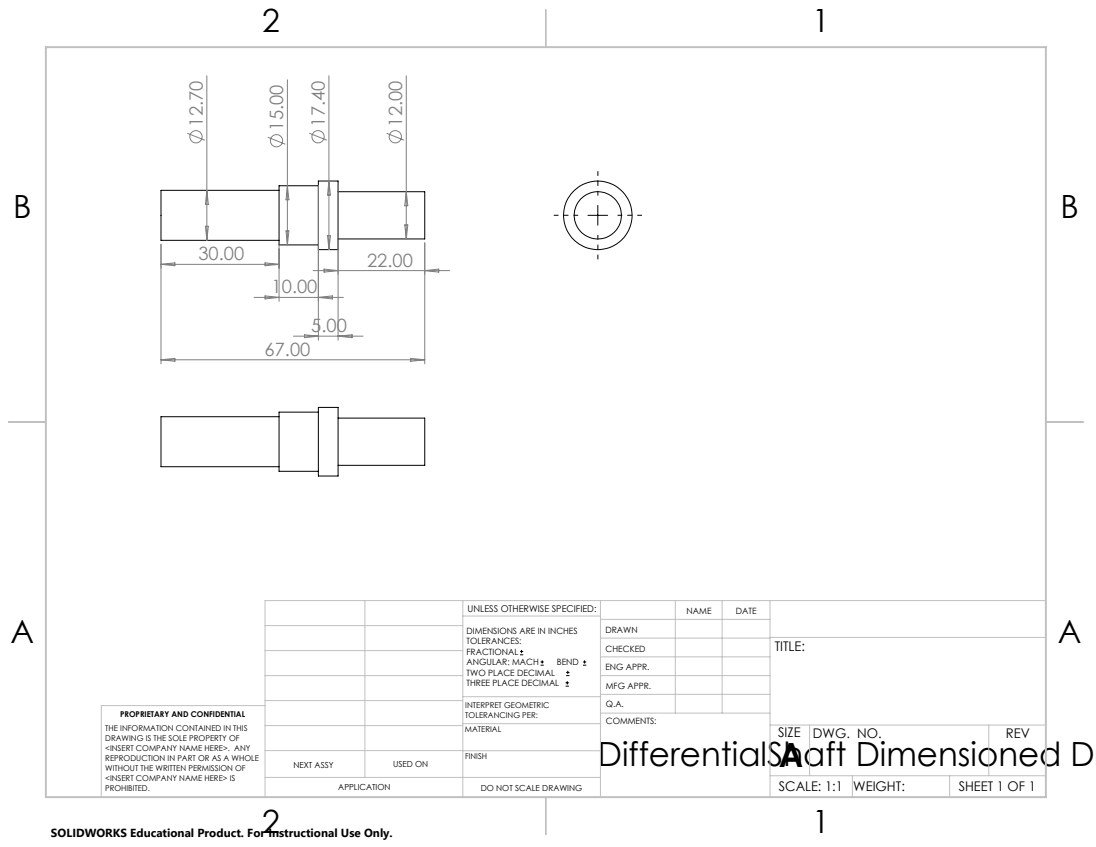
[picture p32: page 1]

UNLESS OTHERWISE SPECIFIED: | | NAME | DATE
DIMENSIONS ARE IN INCHES TOLERANCES: FRACTIONAL ANGULAR: MACH BEND TWO PLACE DECIMAL THREE PLACE DECIMAL | DRAWN

CHECKED | | | TITLE:

ENG APPR.
MFG APPR.

INTERPRET GEOMETRIC TOLERANCING PER: | Q.A.
MATERIAL | | SIZE A | DWG. NO. | REV

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

COMMENTS:
DifferentialShaft Dimensioned Drawing

NEXT ASSY | USED ON | FINISH

APPLICATION | DO NOT SCALE DRAWING | | SCALE: 1:1 | WEIGHT: | SHEET 1 OF 1

SOLIDWORKS Educational Product. For Instructional Use Only.

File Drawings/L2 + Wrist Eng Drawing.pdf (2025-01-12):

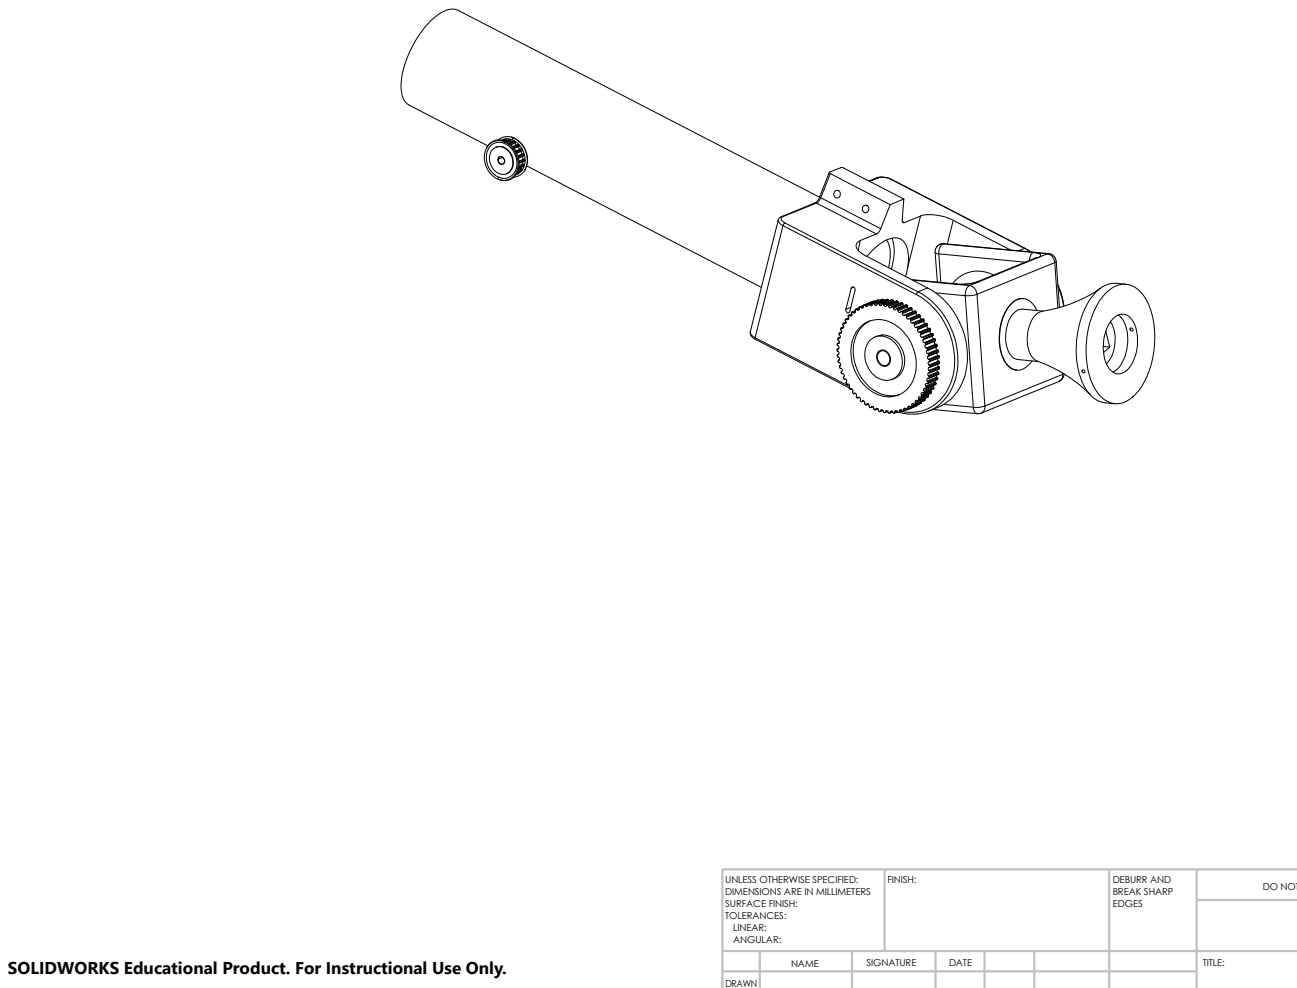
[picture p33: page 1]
DRAWN; FINISH:; EDGES; NAME; SIGNATURE; DATE; TITLE:; DEBURR AND BREAK SHARP

UNLESS OTHERWISE SPECIFIED:
DIMENSIONS ARE IN MILLIMETERS
SURFACE FINISH:
TOLERANCES:
LINEAR:
ANGULAR:

DO NOT SCALE DRAWING

SOLIDWORKS Educational Product. For Instructional Use Only.

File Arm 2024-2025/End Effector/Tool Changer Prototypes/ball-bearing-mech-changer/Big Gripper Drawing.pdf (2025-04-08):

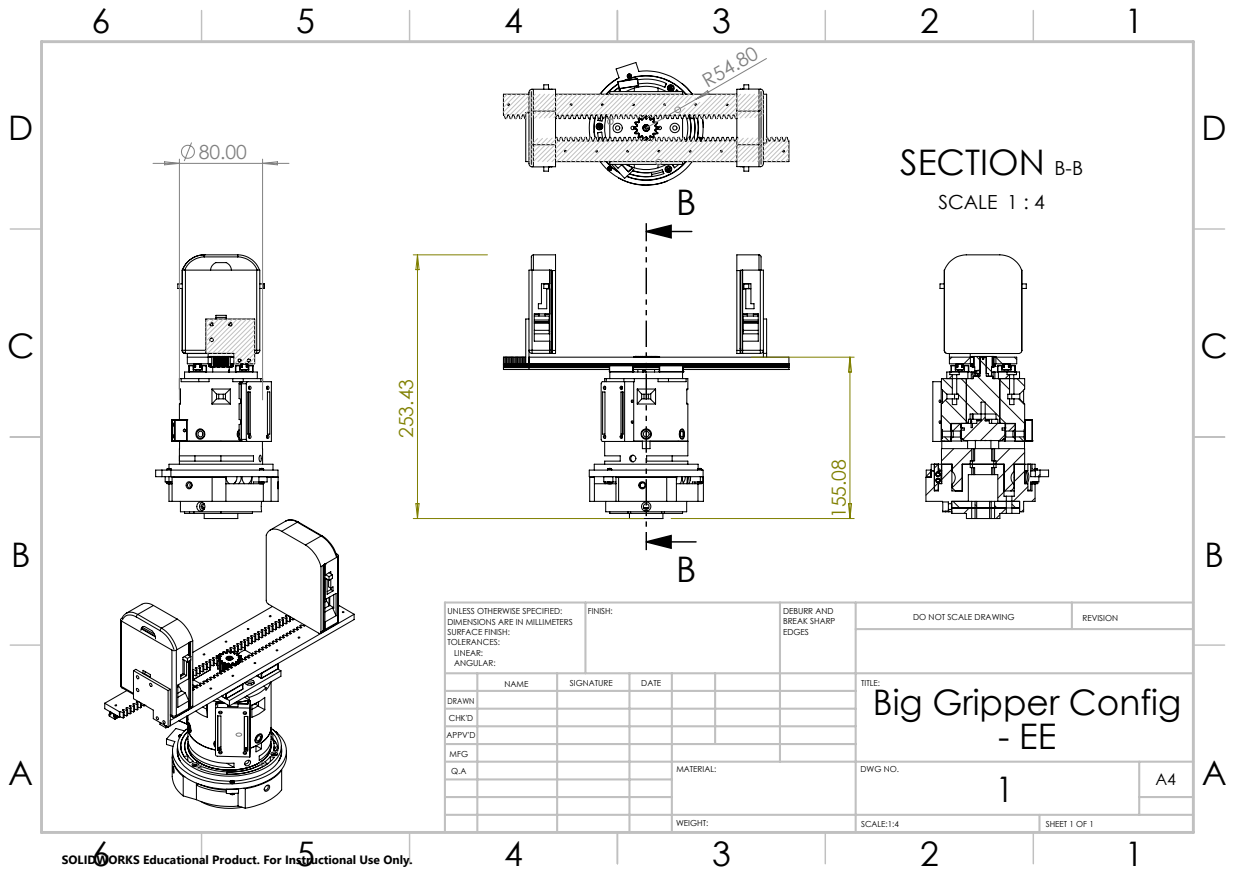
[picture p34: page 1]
SECTION B-B; SCALE 1 : 4; FINISH:; DEBURR AND; BREAK SHARP; DO NOT SCALE DRAWING; REVISION; SCALE:1:4; SHEET 1 OF 1

UNLESS OTHERWISE SPECIFIED:
DIMENSIONS ARE IN MILLIMETERS
SURFACE FINISH:
TOLERANCES:
LINEAR:
ANGULAR:

NAME | SIGNATURE | DATE | | | | TITLE: Big Gripper Config - EE

DRAWN
CHK'D
APPV'D
MFG
Q.A | | | | MATERIAL: | DWG NO. 1 | A4

SOLIDWORKS Educational Product. For Instructional Use Only.

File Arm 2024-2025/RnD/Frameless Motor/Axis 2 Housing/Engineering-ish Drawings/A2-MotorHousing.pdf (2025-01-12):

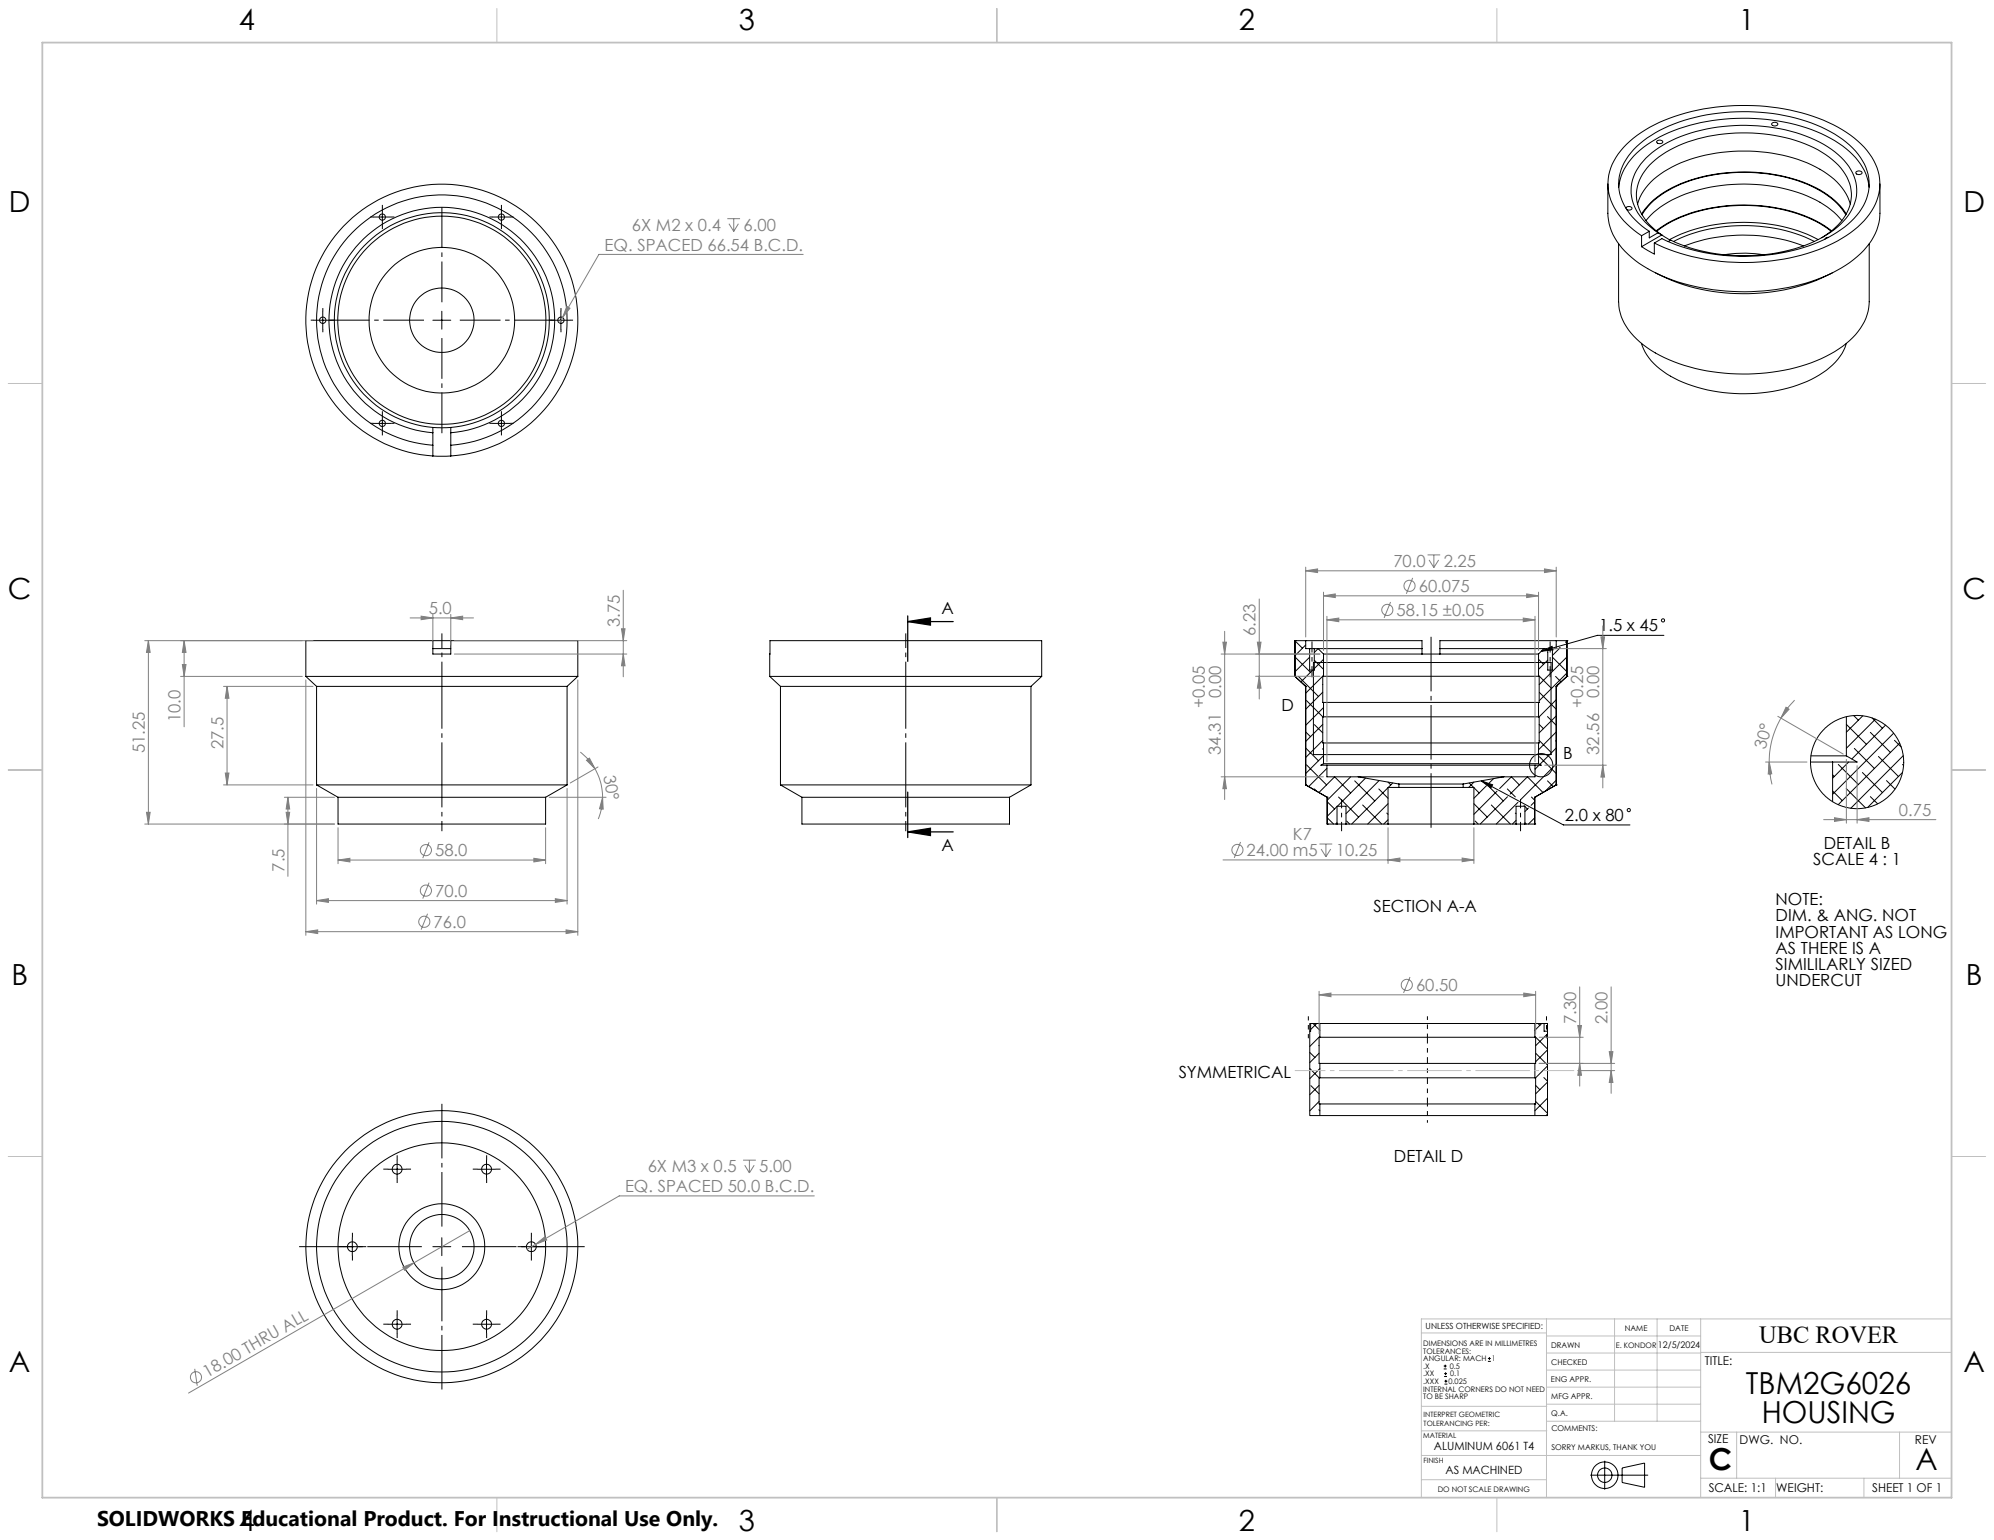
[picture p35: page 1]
6X M2 x 0.4 6.00 EQ. SPACED 66.54 B.C.D.; SECTION A-A; 6X M3 x 0.5 5.00 EQ. SPACED 50.0 B.C.D.; 18.00 THRU ALL; DETAIL D

DETAIL B
SCALE 4 : 1
NOTE:
DIM. & ANG. NOT
IMPORTANT AS LONG
AS THERE IS A
SIMILILARLY SIZED
UNDERCUT

UNLESS OTHERWISE SPECIFIED: | | | DATE | UBC ROVER NAME
DIMENSIONS ARE IN MILLIMETRES TOLERANCES: ANGULAR: MACH 1 .X 0.5 .XX 0.1 .XXX 0.025 INTERNAL CORNERS DO NOT NEED TO BE SHARP | DRAWN | E. KONDOR 12/5/2024

CHECKED | | | TITLE: TBM2G6026 HOUSING

ENG APPR.
MFG APPR.

INTERPRET GEOMETRIC TOLERANCING PER: | Q.A.
MATERIAL ALUMINUM 6061 T4 | SIZE C | DWG. NO. | REV A
AS MACHINED FINISH

COMMENTS:
SORRY MARKUS, THANK YOU

DO NOT SCALE DRAWING | SCALE: 1:1 | WEIGHT: | SHEET 1 OF 1

SOLIDWORKS Educational Product. For Instructional Use Only.

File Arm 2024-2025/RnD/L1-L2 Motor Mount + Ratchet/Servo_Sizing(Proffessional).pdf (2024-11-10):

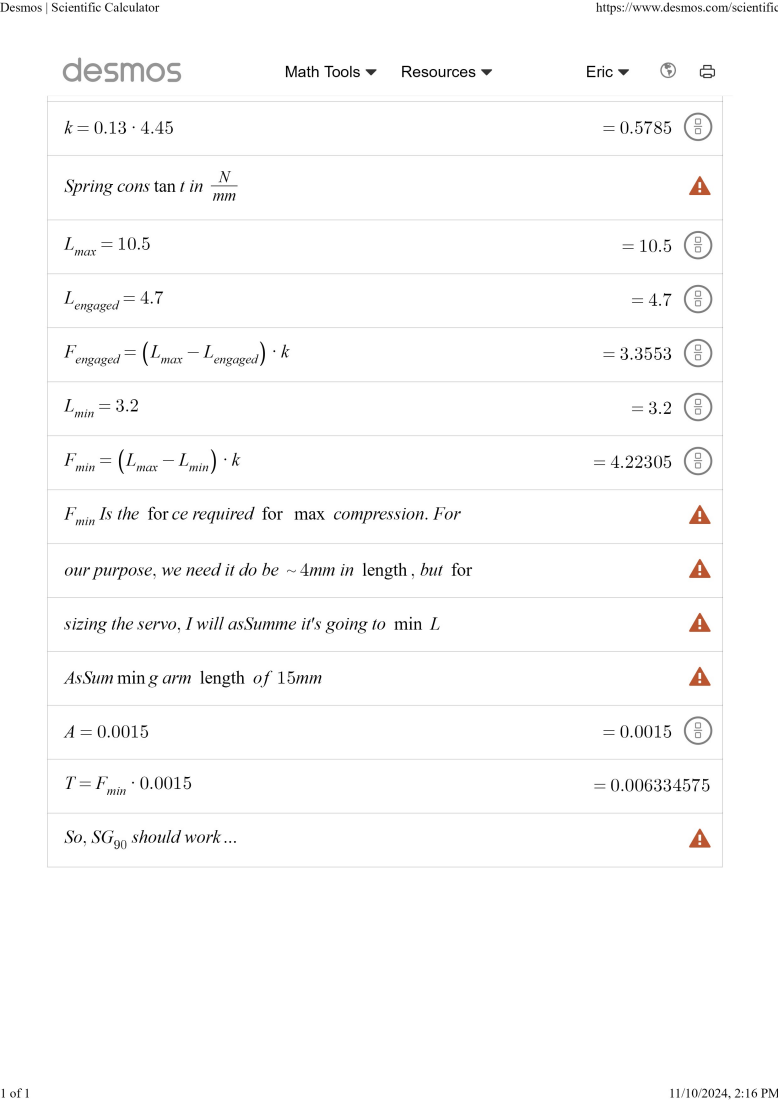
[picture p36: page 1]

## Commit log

2024-07-07 Created repository 1st entry and part
    Committed Link 2 Structural tube as "L2 Structure". Rough CAD to start and not referenced in "Full Arm" assembly.
    [L2 Structure.SLDPRT]
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2024-07-14 L2 and Wrist Assemblies Started
    Created more assemblies for link 2 and wrist. Started creating the upright CAD
    [Encoder AMT102.SLDPRT, L2 + Wrist.SLDASM, L2 Structure.SLDPRT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]
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2024-07-20 Added motor mount for Nema 11 to wrist
    Designed to mount a Nema 11 motor to the smooth end of a bevel gear.
    The large flat end is meant to rub against a smooth bearing to help stabilize the mount. Additionally, it is intended that the mount be pinned through the bevel gear.
    [RV-0009.SLDPRT]
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2024-07-21 Added Gears, Changed Uprights Slightly
    Modelled the gear off the drawings and added to assembly.
    Made the structure thicker for the uprights with plans to refine.
    Changed the centre configuration for both covered.
    [Centre_Block_Differential_Centre.SLDPRT, L2 + Wrist.SLDASM, L2 Structure.SLDPRT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]
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2024-07-28 RV-0005-02
    Adjusted A6 housing to allow for larger gear
    Added nut/bolt holes to allow for manufacturing
    [RV-0005.SLDPRT, RV-0009.SLDPRT]
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2024-08-04 Changed Upright, added wrist rod
    Made the shape of the upright different and made a centre opening bigger than necessary. Made and added a rod part to use for dimensioning/placement.
    [Centre_Block_Differential_Centre.SLDPRT, L2 + Wrist.SLDASM, PM3-25 Copied.SLDPRT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]
2024-08-08 Added Bearings, added another gear
    Modelled and added into the assembly an appropriately sized gear. May have to resize when looking closer at the specs again. Also have to redo the dependencies in the uprights.
    [L2 + Wrist.SLDASM, PM3-25 Copied.SLDPRT, Sealed Bearing 15mm.SLDPRT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]
2024-08-11 Renamed Parts in Assembly, Changed Upright Slightly
    Renamed a few parts to the according part number. Changed the sizing of the upright to better fit the bearings.
    [L2 + Wrist.SLDASM, PM3-25 Copied.SLDPRT, RV-0003_Bevel-Shafts.SLDPRT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]
2024-08-13 CAD for tool changer prototype following smartshift design
    Edited name of EE text file
    Added CAD for a tool changer prototype I am working on
    There is not really any good documentation for it, best right now is in the meeting notes for Week of 8/12/2024
    [Bottom-Baseplate.SLDPRT, Bottom-Baseplate.STEP, Bottom.SLDPRT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]
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2024-08-15 Updated SlideSwap Tool Changer
    Edited the sliding magnet thing and made lots of minor changes
    Added some coloring in the files so the assembly is more organized
    New cad file for sliding magnet cover, new 3d print files are there as well.
    [Bottom-Baseplate.SLDPRT, Bottom.SLDPRT, Combined Sliding Tool Changer.SLDASM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]
2024-08-16 Updated Bottom and Made New Sliding Insert
    Updated bottom -- added screw holes
    Made new sliding magnet holder -- this one has a tab that inserts from the side
    [Bottom.SLDPRT, Bottom.STEP, Combined Sliding Tool Changer.SLDASM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]
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2024-08-18 L2 Tube and Upright Minor Changes
    Lengthened and changed the size of link 2 for the appropriate beam bending analysis. Added a slot for tensioning and tightened the dims for the upright to wrist.
    [L2 + Wrist.SLDASM, L2 Structure.SLDPRT, Link 2 Assembly.SLDASM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]
2024-08-19 Rollback on update to top
    Update to top resulting in sliding magnet getting stuck sometimes.
    [Top.SLDPRT]
2024-08-19 Part way implementation of chassis locking mechanism
    Part way implementation of chassis locking mechanism. Currently it needs to be modified to allow for smoother mechanical transfer.
    [Attachment Point for Device.SLDPRT, Bottom.SLDPRT, Combined Sliding Tool Changer.SLDASM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]
2024-08-20 Ball bearing tool changer - Added EE holder (chassis part)
    Also edited assembly and changed some dimensions
    [EE-attachment-part.SLDPRT, EE-holder-Chaissis.SLDPRT, ball-Bearing-holder.SLDPRT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]
2024-08-20 Ball-bearing tool changer
    changed tolerances and EE holder, also changed 15mm to 14mm ball bearings
    [14mm ball-bearing.SLDPRT, 15mm ball-bearing.SLDPRT, EE-attachment-part.SLDPRT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]
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2024-08-29 Added internal uprights to link 2 assem
    The fillets are rlly aggresive ik, but it's sort of a reminder that it's unfinished. The one thing that needs to be done still is to increase the hole size on all of the bevel gear holes (two feature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
    [Internal_Uprights.SLDPRT, L2 + Wrist.SLDASM, RV-0006 Copied.SLDPRT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]
2024-09-01 A few Changes for Ball Bearing Tool Changer
    1. Added mounts for Pogo Pin & hall effect sensor
    2. Changed hole sizes to M3
    3. Reduced thickness of ball bearing holder
    4. Added holes for EE part for strength testing
    5. Adjusted spring mount diameter
    [EE-attachment-part.SLDPRT, ball-Bearing-holder.SLDPRT, slider-constraints.SLDPRT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]
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2024-09-10 Chassis Holder and updates for the rest to allow for it
    Chassis Holder and updates for the rest to allow for it
    [Attachment Point for Device.SLDPRT, Bottom.SLDPRT, Combined Sliding Tool Changer.SLDASM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]
2024-09-11 Added Magnet Sensor to Repo failsafe added to smartshift holder
    Magnet sensor added and failsafe added to smartshift toolchanger
    [A1301-2 - Sensor.SLDPRT, Attachment Point for Device.SLDPRT, Bottom-Baseplate.SLDPRT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]
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2024-09-11 Changes to tool changer
    -changed spacing of pins
    -renamed all parts
    -added fail-safe
    -changed the ball bearing holder to include bottom slot
    [BT-0001.SLDPRT, BT-0002.SLDPRT, BT-0003.SLDPRT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]
2024-09-12 File management
    Redid the storage system for 3D prints within the slideshift mechanical tool changer prototype
    [Attachment Point for Device.STL, Bottom-Baseplate.STEP, Bottom-Baseplate.STL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]
2024-09-30 Ball Bearing Tool Changer-Modification
    -Resized slider to fit spring
    -added guides for springs
    -adjusted dimensions for ball bearings to fit
    [BT-0001.SLDPRT, BT-0001.STL, BT-0002.SLDPRT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]
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2024-10-04 Link 1 to Link 2 Motormount/connection
    This is the motor mount that will also act as the link 1 to link 2 connection. The bottom plate will screw into the main link 1 shaft (using countersunk screws) and then the motor will go on the L1-L2 bracket. Depending on the gearbox, I imagine the mounting holes will be different, but it should look similar. We use a similar setup at my work, and we just have a 3D printed negative underneath to help with motor sag.
    Then, in the indent, there will be a thrust bearing to handle the moment from the weight of link 2.
    Thanks
    [L1-L2-Bracket.SLDPRT, L1-L2-Plate.SLDPRT, L1-L2-Truss.SLDPRT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]
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2024-10-04 Link 2 changes
    Made link 2 cut, made a plate for nema 11, made a start for mounting position. All of this should be discussed at meeting tomorrow because the link is kind of scaring me just with fitting two motors 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
    [L2 Structure_cut.SLDPRT, Nema_11_faceplate.SLDPRT, plate_to_link_mount_v1.SLDPRT]
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2024-11-05 last second fixes
    [AviatorFrame.SLDPRT, DM320.SLDPRT, DM320Frame.SLDPRT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]
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2024-12-03 Added shaft
    Needs some fixing. committing so I can backtrack if needed (point of github I suppose)
    [Lid_MotorSide.SLDPRT, Motor-Shaft-Proto.SLDPRT, Motor_Housing-Proto.SLDPRT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]
2024-12-03 Adjusted motor housing & shaft
    Think the shaft and housing are complete-ish (still need to add corner relief in housing)
    Biggest thing left is to fix the top lid (make it interface with the top bearing) and make the bottom lid. Have to consider assembly during this as well to maintain axial alignment
    Might also adjust the housing so it's more snug on the bottom bearing, back have to think about it.
    Also made all the equations off a text document which is pretty cool. Don't know why it didn't default to excel, but it is what it is ig.
    [Lid_MotorSide.SLDPRT, Motor-Shaft-Proto.SLDPRT, Motor_Housing-Proto.SLDPRT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]
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2024-12-05 Added drawing for A2 Motor Housing
    Hopefully tolerances are ok...
    [A2-MotorHousing.SLDDRW, A2-MotorHousing.SLDPRT, Front-View-Check.SLDPRT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]
2024-12-05 Fixed(?) Drawing (def improved)
    [A2-MotorHousing.SLDDRW, A2-Shaft.SLDPRT, Front-View-Check.SLDPRT]
2024-12-05 Adjusted some dimensions and tolerances
    [A2-MotorHousing.SLDDRW]
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2024-12-10 Adjusted some tolerances
    [A2-MotorHousing.SLDDRW]
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2025-01-26 V2
    Need to add motor + tolerances, but otherwise should work?
    [11HS12-0674D-PG27.SLDPRT, 166164_GP32A-3st.SLDPRT, 166164_GP32A-3st.stp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]
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2025-01-26 Fixed File Directory of Gear
    [A4.SLDASM, SI0_5-80_On.sldprt]
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2025-01-28 Fixed Length, Holes
    Added holes to cover, fixed length of middle part
    [A4.SLDASM, Cover.SLDPRT, MiddlePart.SLDPRT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]
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2025-02-04 Changes to Uprights In+Out
    Made changes to the uprights according to the gears and tried to find what the timing belt length will be.
    Seems there are issues with the CAD or calcs somewhere as this is much longer than expected.
    [A1-Assem.SLDASM, Internal_Uprights.SLDPRT, Link2-Assem.SLDASM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]
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2025-02-07 L2 modifications
    Made some minor measurements and changes to spacing. Also, broke some more stuff in the wrist and uprights.
    [Link2-Assem.SLDASM, RV-0012_Wrist-Upright.SLDPRT]
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2025-02-23 "finished" A1 plate attatchment
    Need to check screw heads don't interfere.
    [(2023 Ver) 2025 Arm Plate.SLDPRT, A1-Assem.SLDASM, A1-Bearing-Support.SLDPRT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]
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2025-03-02 Fixed arms position on chassis plate
    [(2023 Ver) 2025 Arm Plate.SLDPRT]
2025-03-02 Double fixed link 1 position on arm plate
    [(2023 Ver) 2025 Arm Plate.SLDPRT]
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2025-03-03 Shortened Middle Part
    [A4 (March 2).SLDASM, Cover2.SLDPRT, MiddlePart2.SLDPRT]
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2025-03-06 Added Link 2 to A4
    As title. Had to just hide the temp pipe for now because it is a fixed mate + the origin of the A4 assembly. Can be fixed later.
    [A1-Assem.SLDASM, A1-Plate.SLDPRT, A1-Side-Plate-Harm.SLDPRT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]
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2025-03-06 Weird Backups + Upright Rebuild Fixed
    Had some weird backups saved that Github will be removing.
    Hate the upright build and also finally fixed the rebuild issues. I wish I had made this better initially.
    [RV-0012_Wrist-Upright.SLDPRT]
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2025-03-06 Made all Link 1 holes correct size
    Add limit switches and finalize their positions.
    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
    [A1-Assem.SLDASM, A1-Plate.SLDPRT, A1-Side-Plate-Harm.SLDPRT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]
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2025-03-09 FIXING GABRIELS MESSUP >:(
    NO COLONS!!!!!
    [BT-0004.DXF]
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2025-03-09 Flipped Plate and Added Limits
    [(2023 Ver) 2025 Arm Plate.SLDPRT, 91290A306_Alloy Steel Socket Head Screw.SLDPRT, A1-Assem.SLDASM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]
2025-03-09 Fixed A1 print thing.
    [A1-Bearing-Support.SLDPRT]
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2025-03-16 Revert "Merge branch 'main' of https://github.com/UBC-Snowbots/Arm"
    This reverts commit 55302e57cf84dcaac106093ea9c3ed196f149cf7, reversing
    changes made to 22ba305cde8b13c4fc4e4449f1ca68f553a0d6a6.
    [2485N242_Metal Gear Rack - 20 Degree Pressure Angle.SLDPRT, 2485N242_Metal Gear Rack - 20 Degree Pressure Angle.STEP, 2664N423_Metal Gear - 20 Degree Pressure 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]
2025-03-19 reverted gripper mechanism
    [2485N242_Metal Gear Rack - 20 Degree Pressure Angle.SLDPRT, 2485N242_Metal Gear Rack - 20 Degree Pressure Angle.STEP, 2664N423_Metal Gear - 20 Degree Pressure 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]
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2025-03-20 Fixed link2 assmbly
    made some changes and fixed motor mounting now will work on some optimization and motor mounting pla part
    [Link2-Assem.SLDASM]
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2025-03-23 Fixed Camera Mount Holes
    [A1-Assem.SLDASM, A1-Plate.SLDPRT, A1-Side-Plate-Harm.SLDPRT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]
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2025-03-23 Added Limited Switch
    Added the limit switch - tight fit!
    [A4 (March 2).SLDASM, Cover2.SLDPRT, LimitSwitches.SLDPRT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]
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2025-03-25 Fixed Upright Mate
    [Slider assembly.SLDASM, Tool Changer With End Effector Assembly.SLDASM, ball bearing mechanism.SLDASM]
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2025-03-30 Matt fixed link 2 and uprights
    [A1-Assem.SLDASM, A1-Plate.SLDPRT, A1-Side-Plate-Harm.SLDPRT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]
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2025-04-02 added waterjet files and fixed precision gripper assem
    [BT-0008-Baseplate.DXF, link-precision gripper.DXF, plate for rail and motor attachment.DXF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]
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2025-04-06 fixed (fingers crossed)!!
    [2664N323_Metal Gear - 20 Degree Pressure Angle2.SLDPRT, A1-Assem.SLDASM, A1-Plate.SLDPRT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]
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2025-04-06 Fixed internal uprights
    [Internal_Uprights.SLDPRT]
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2025-04-08 Fixed EE Problem in the main assembly
    [A1-Assem.SLDASM, A1-Plate.SLDPRT, A1-Side-Plate-Harm.SLDPRT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]
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2025-04-08 Added Final Tolerances
    [A4 (March 2).SLDASM, Cover2.SLDPRT, Endcap2.SLDPRT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]
2025-04-08 Fixed fastener hole issues
    Matt I need your wire holder plz
    [A4 (March 2).SLDASM, Link2-Assem.SLDASM, SI0_5-80_On2.SLDPRT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]
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2025-04-17 fixed sorry!
    [link2_tube.SLDDRW, link2_tube.SLDPRT]
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2025-06-22 Made New Arm Base Plate to Align with Chassis
    Copied dimensioning and moved Base hole further away from Chassis attachment for clearance of A1 attachment plate
    [(2023 Ver) 2025 Arm Plate.SLDPRT, A1-Assem.SLDASM, New Arm Base Plate.DXF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]
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2025-07-07 Small corrections
    [A3-Shaft-Harm-Couple-Spacer.DXF, Harm-Stator-Mount.SLDPRT]
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2025-07-11 Adjusted A56 spacer for tolerance
    [new_A56_spacer.SLDPRT]
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2025-07-14 Added slots to motor mounting for A5/6
    As per title, made the slot 2.5mm in width, m3 clearance
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2025-07-19 Increased Tolerance on Cover2
    [A4 (March 2).SLDASM, Cover2.SLDPRT, Link2-Assem.SLDASM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]
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2025-07-20 Added tolerance to part
    [Bearing-Holder.SLDPRT]
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2025-07-25 Fixed and updated spacer, added new mirrored spacer for A56
    [new_A56_spacer.SLDPRT, new_A56_spacer_mirrrored.SLDPRT]
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2025-07-29 Rotated bolt circle for A4 motor to correct orientation
    As per title, changed bolt circle for mounting gearbox to assembly.
    Angle for bolt circle is 22.5 degrees.
    [A4 (March 2).SLDASM, MotorHolder2.SLDPRT]
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2025-07-30 Revised 56 spacer and bolt holder to not interfere on 1 side
    [A56SpacerFastenerHolder.SLDPRT, new_A56_spacer.SLDPRT]
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2025-08-01 A4 motor bolt side change and spaced the front shoulder
    Changed the side the bolts go in on for the A4 motor bolts at the bottom of the part
    Changed how much thickness the front shoulder has to avoid rubbing of plastic on plastic
    [Cover2.SLDPRT, CoverLeft.SLDPRT, CoverRight.SLDPRT]
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2025-08-01 Revert "Changes to A4 parts"
    This reverts commit de2a564f398eb7e98c71f110774800405bb4ec18.
    [MotorHolder2.SLDPRT, gear-holder2.SLDPRT]
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2025-08-01 increased tolerance on motor mount EE
    [2485N242_Metal Gear Rack - 20 Degree Pressure Angle.SLDPRT, Assembly for big gripper attachment.SLDASM, Big Gripper Motor Assy.SLDASM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]
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2025-08-02 Changes to tolerances
    [A56_Driver_Holder_Top_Part.SLDPRT, A56_Driver_Holder_Top_assm.SLDASM, A56_Driver_Holder_part.SLDPRT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]
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2025-08-04 Updates to uprights - reinforcement, and A4 - better motor mount locating
    [A4 (March 2).SLDASM, Bearing-Holder.SLDPRT, Cover2.SLDPRT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]
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2025-08-05 Corrections to uprights, improvements to all A4 parts
    [A4 (March 2).SLDASM, Centre_Block_Differential_Centre.SLDPRT, Cover2.SLDPRT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]
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2025-08-05 Revert "Merge branch 'main' of https://github.com/UBC-Snowbots/Arm"
    This reverts commit 9709d0c084b6a82e89b83b27c4397abdf6e829d0, reversing
    changes made to 1c64c792029a4a573f92127705bb17b640a4491a.
    [new_A56_spacer_mirrrored.SLDPRT]
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2025-10-04 fixed typo in 2026/EE/PCB/readme.md
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2025-10-04 redid pcb dir managment, with hopefully working shortcuts
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2025-10-09 Fixed up some assembly for EE tool rack
    [Assem3.SLDASM, BT-0005.SLDPRT, CHASSIS MOUNT V2.SLDPRT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]
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2025-10-15 Change Core-xy Mounting Hole Heat Insert Fix
    Changed the mounting holes and cover profiles for core-xy pla components
    [6709K143_55 mm Long x 9 mm Wide Standard Guide Rail for Ball Bearing Carriage.SLDPRT, Bottom left pivot housing.SLDPRT, Core XY Assembly Mk2.SLDASM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]
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2025-10-21 Fixed Link 2 Assembly, Edited Uprights
    [A1-Assem.SLDASM, A1-Plate.SLDPRT, A1-Side-Plate-Harm.SLDPRT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]
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2025-10-31 Prototyping for Wrist Differential Issues
    [Middle Bearing Holder Prototype.SLDPRT, Wrist-Upright_Right Prototype Design.SLDPRT]
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2026-01-05 Fixed some rebuild errors on tool changer assembly
    [BT-0001.SLDPRT, Big Gripper Motor.SLDPRT, MirrorTool insert part.SLDPRT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]
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2026-02-01 Fixed alignment of cut (for motor holder) in Cover2 and size of endcap tabs
    [Cover2.SLDPRT, CoverLeft.SLDPRT, CoverRight.SLDPRT]
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2026-02-01 Revert "Merge branch 'main' of https://github.com/UBC-Snowbots/Arm"
    This reverts commit 57dec2b6dc0639c9dbc4c20a36c1ea615bc0937e, reversing
    changes made to 49c4b6ad552ed8fb26bb0aa560f1eff4286778c6.
    [6709K152_275 mm Long x 9 mm Wide Standard Guide Rail for Ball Bearing Carriage.SLDPRT, Assembly for big gripper attachment.SLDASM, BIg_gripper_tool_attachment.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]
2026-02-01 Revert "Fixed alignment of cut (for motor holder) in Cover2 and size of endcap tabs"
    This reverts commit 49c4b6ad552ed8fb26bb0aa560f1eff4286778c6.
    [Cover2.SLDPRT, CoverLeft.SLDPRT, CoverRight.SLDPRT]
2026-02-01 Fixed alignment of cuts in Cover2 and changed size of endcap tabs
    [A1-Assem.SLDASM, A4 (March 2).SLDASM, Assembly for big gripper attachment.SLDASM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]
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2026-03-08 fixed big gripper assembly
    [Assembly for big gripper attachment.SLDASM, Finger_Backing.SLDPRT, Fingers.SLDASM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]
2026-03-08 Mating error?
    [Slider assembly.SLDASM, Tool Changer With End Effector Assembly.SLDASM, ball bearing mechanism.SLDASM]
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2026-03-21 Fixed Tabs
    Fixes A2 Tabs to have clearance holes on the straps rather than tapped holes.
    [A1-Side-Plate-Crosslink.SLDPRT, A4 (March 2).SLDASM, Link2-Assem.SLDASM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]
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2026-03-22 Link-dos Fix
    Added the ID cut to accomodate the ring gear.
    [A4 (March 2).SLDASM, SI0_5-80_On2.SLDPRT, link2_tube-OLD.SLDPRT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]
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2026-05-21 Fixed inserts for EE PCB holder
    [A1GearboxAssem.SLDASM, A1_Moteus_Holder.SLDPRT, A356_Driver_Holder_part.SLDPRT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]
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2026-05-26 EE_testing stand+ fixed arm assembly+ changed uprights
    [A1-Assem.SLDASM, A1-Plate.SLDPRT, A1-Side-Plate-Harm.SLDPRT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]
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
